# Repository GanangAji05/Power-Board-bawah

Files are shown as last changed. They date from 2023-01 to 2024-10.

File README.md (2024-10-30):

# Power-Board-bawah

Design PCB



Design 3D



Check signal PWM
IMG-20240414-WA0002

Testing Motor and code

https://github.com/user-attachments/assets/2eb00f5d-e821-4132-b0ed-e6486bcefb03

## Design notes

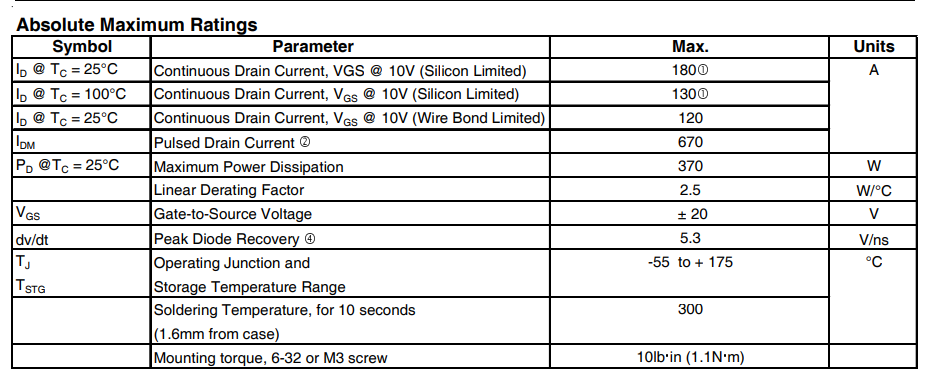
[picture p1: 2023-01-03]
docs/mosfets/irfb4110.png

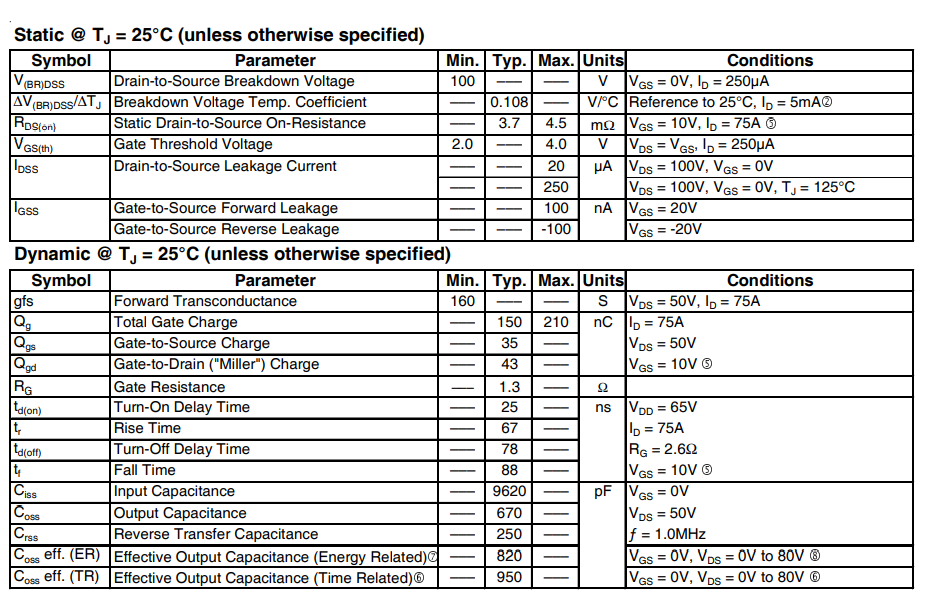
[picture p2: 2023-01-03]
docs/mosfets/irfb4110-2.png

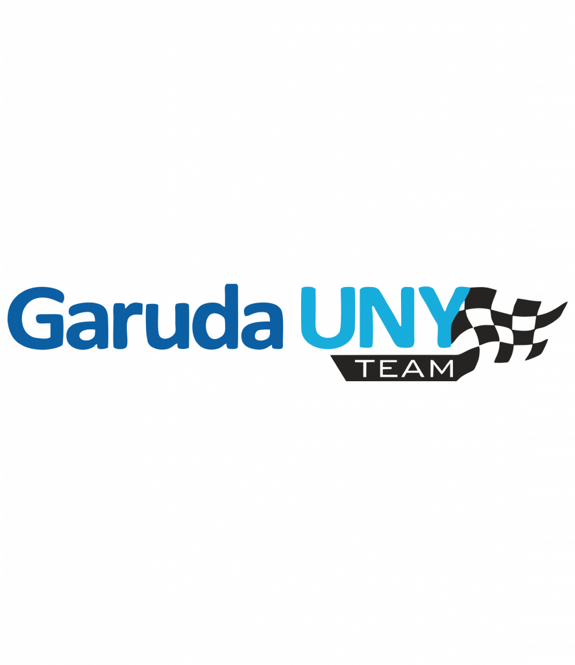
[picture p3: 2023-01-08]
external_cad_lib/garuda-886x1024.png

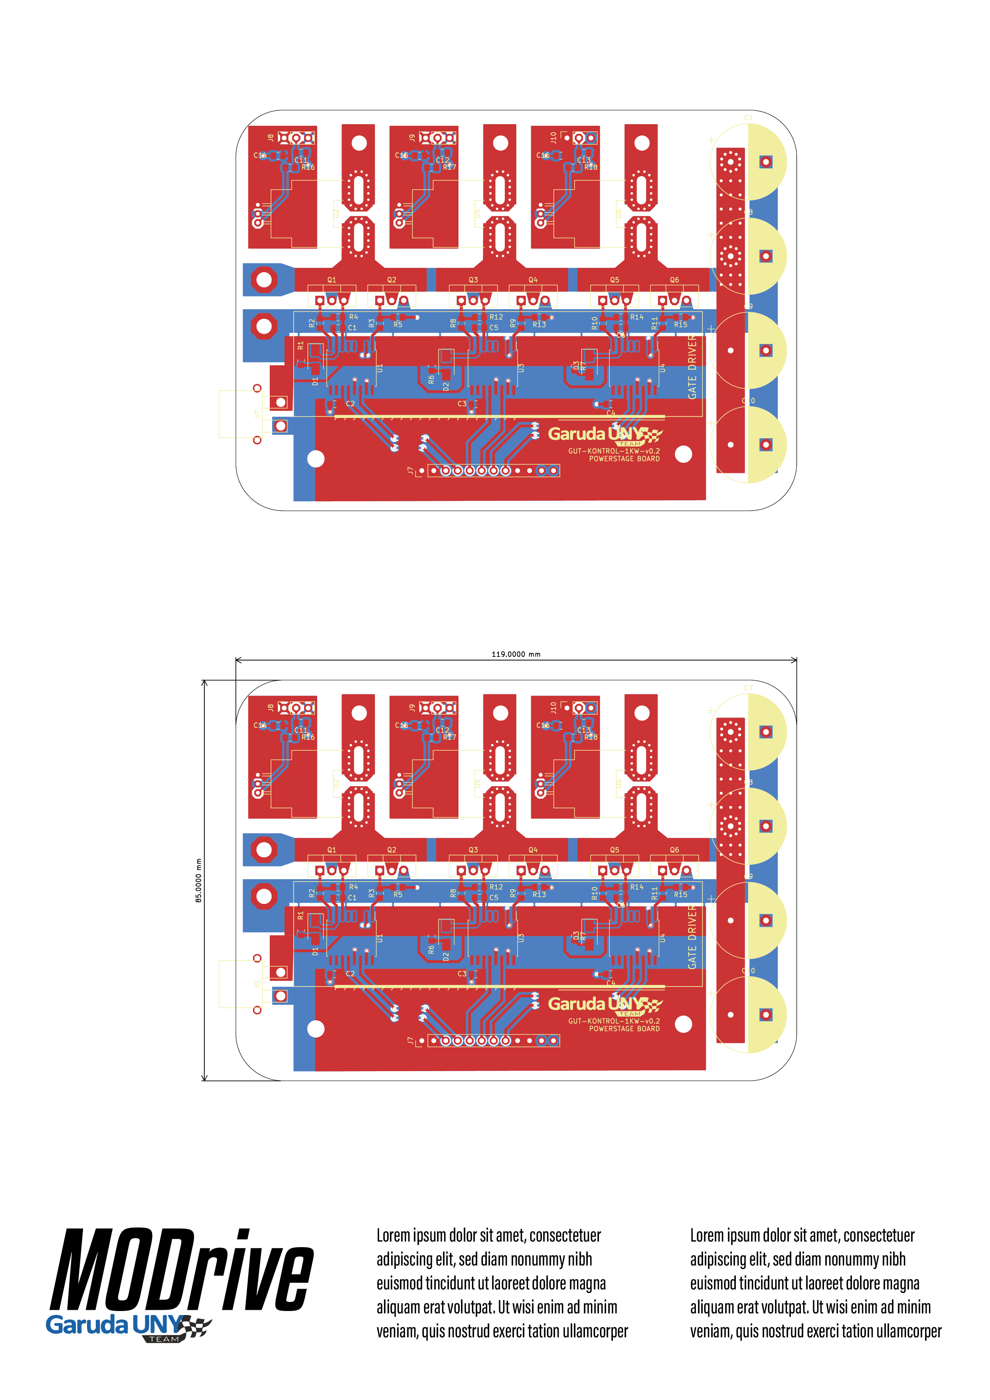
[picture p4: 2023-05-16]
artwork/pcb_artwork-01.png

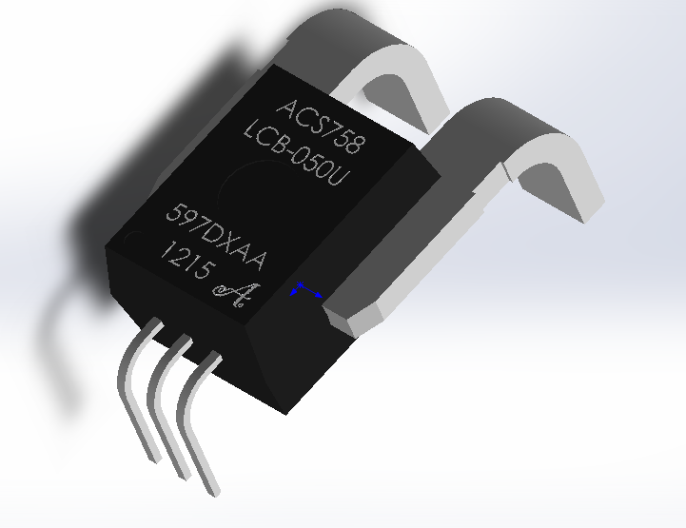
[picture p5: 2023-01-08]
external_cad_lib/acs758-1.snapshot.2/Renderings/Безымянный.png

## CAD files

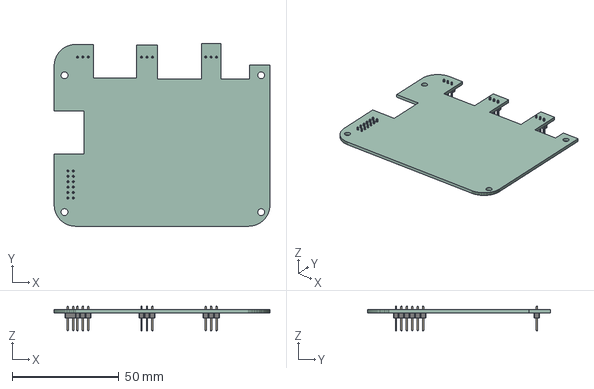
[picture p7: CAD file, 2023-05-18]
dats-kontrol-1kw-sysmin.step
101.0 x 85.4 x 11.5 mm
PCB

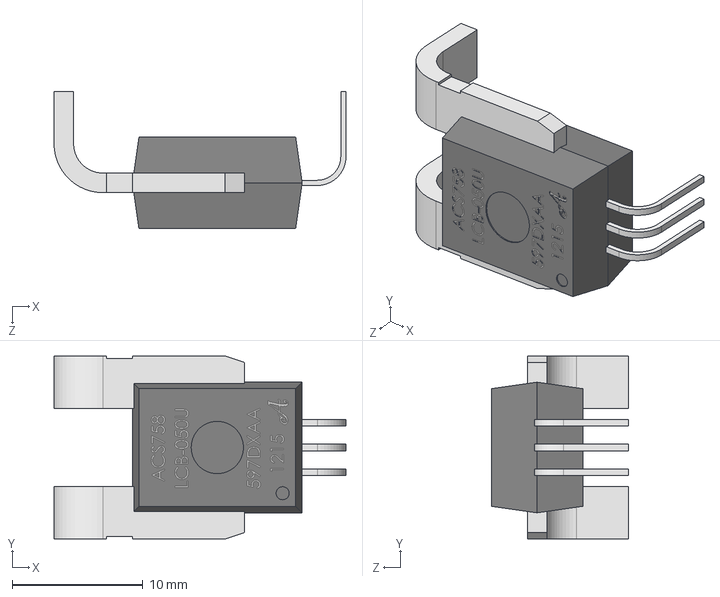
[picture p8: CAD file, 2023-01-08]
external_cad_lib/acs758-1.snapshot.2/ACS758.STEP
22.4 x 14.0 x 10.5 mm

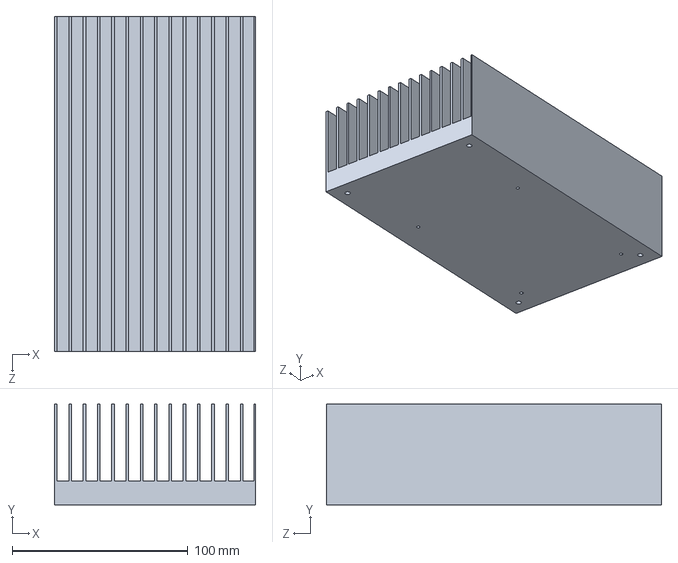
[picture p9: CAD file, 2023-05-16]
external_cad_lib/heatsink.STEP
114.3 x 57.1 x 190.5 mm

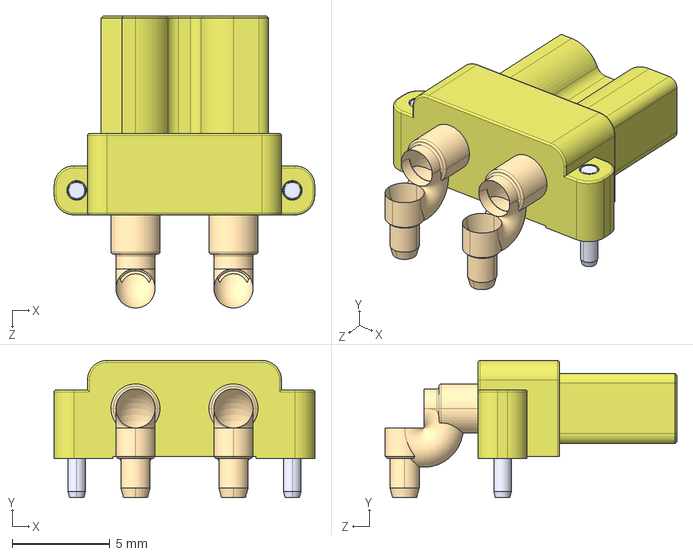
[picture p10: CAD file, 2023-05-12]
external_cad_lib/XT30PW-F/XT30PW-F.step
13.3 x 7.00 x 14.9 mm

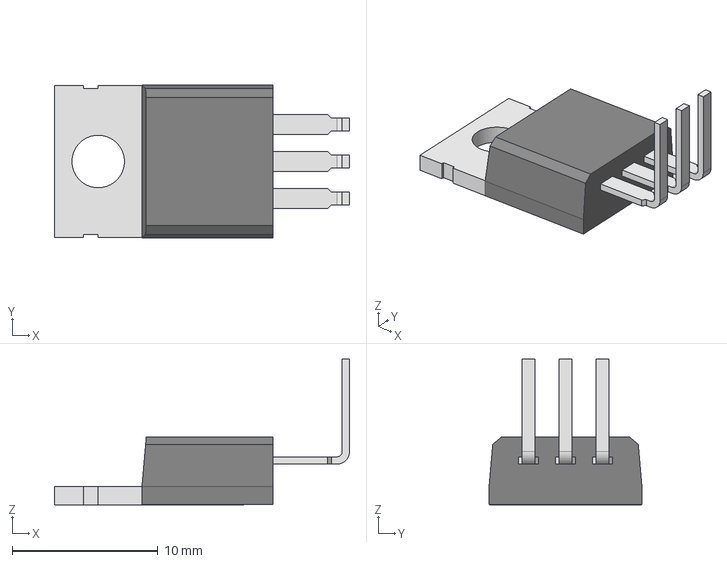
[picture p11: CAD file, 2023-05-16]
external_cad_lib/TO-220_horizontal_back_line.stp
20.2 x 10.5 x 10.0 mm

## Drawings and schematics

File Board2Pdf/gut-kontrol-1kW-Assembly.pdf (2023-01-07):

1 | 2 | 3 | 4 | 5 | 6

A

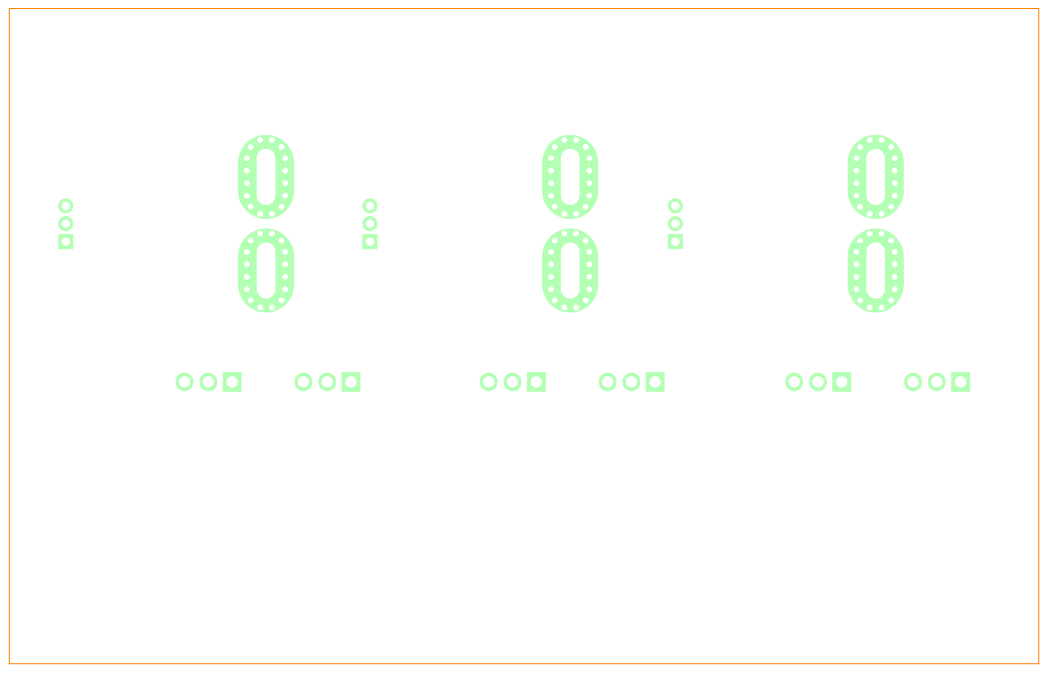
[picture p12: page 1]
D Date: KiCad E.D.A. kicad (6.0.10) Size: A4; Rev:

File: gut-kontrol-1kW.kicad_pcb Sheet: ColoredBottom
Id: 1/1 Title:

1 | 2 | 3 | 4 | 5 | 6

A

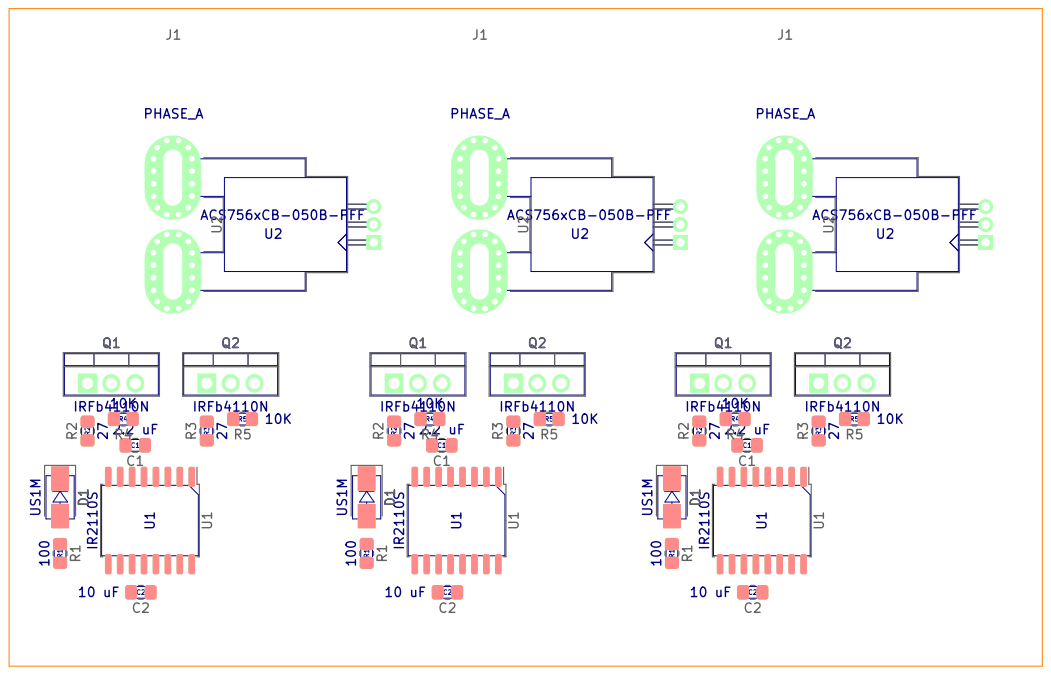
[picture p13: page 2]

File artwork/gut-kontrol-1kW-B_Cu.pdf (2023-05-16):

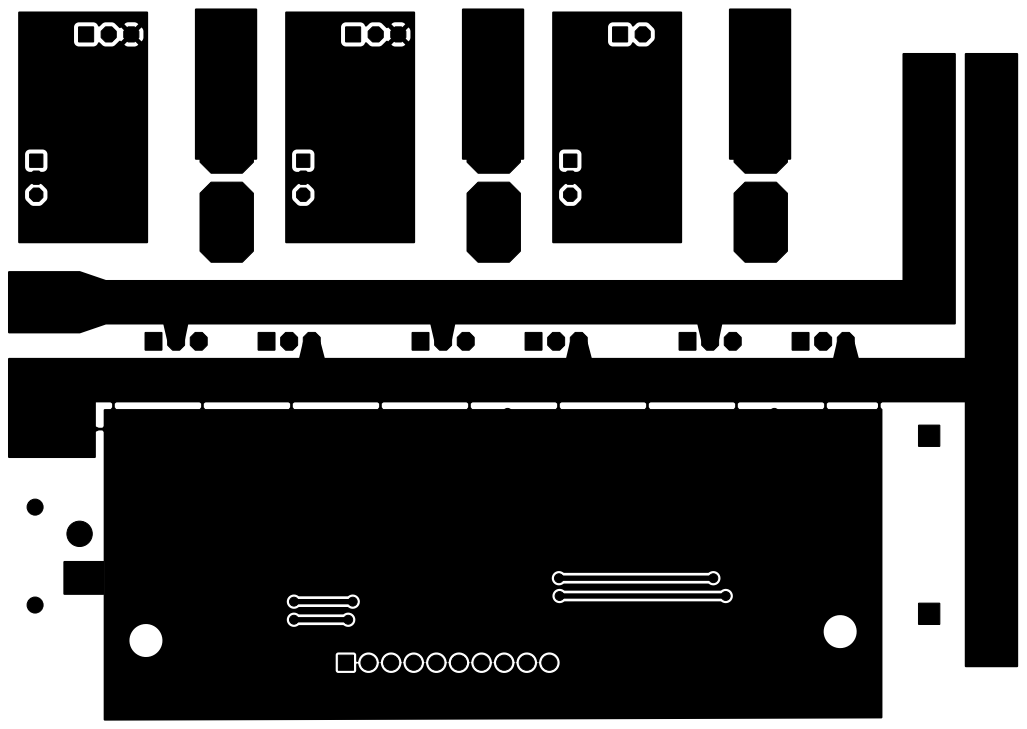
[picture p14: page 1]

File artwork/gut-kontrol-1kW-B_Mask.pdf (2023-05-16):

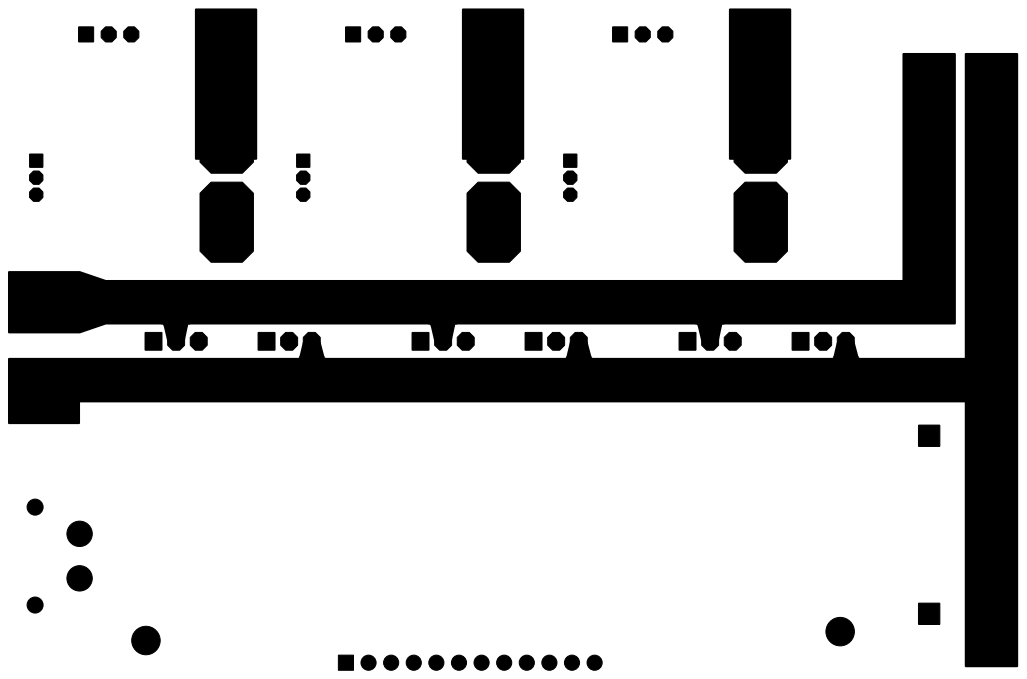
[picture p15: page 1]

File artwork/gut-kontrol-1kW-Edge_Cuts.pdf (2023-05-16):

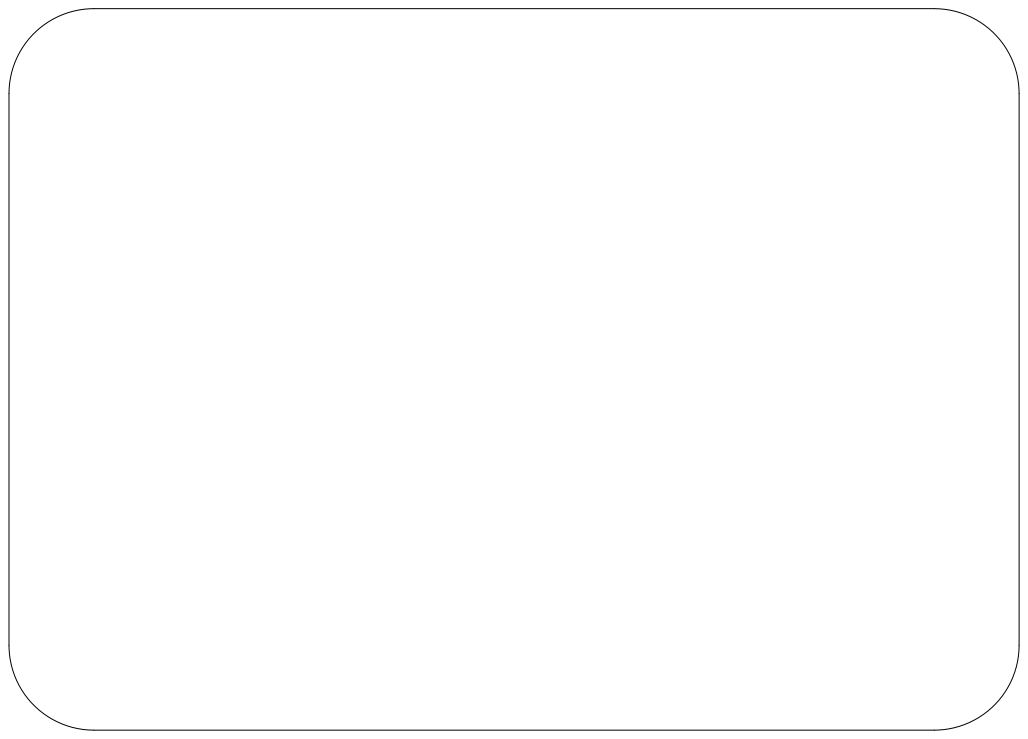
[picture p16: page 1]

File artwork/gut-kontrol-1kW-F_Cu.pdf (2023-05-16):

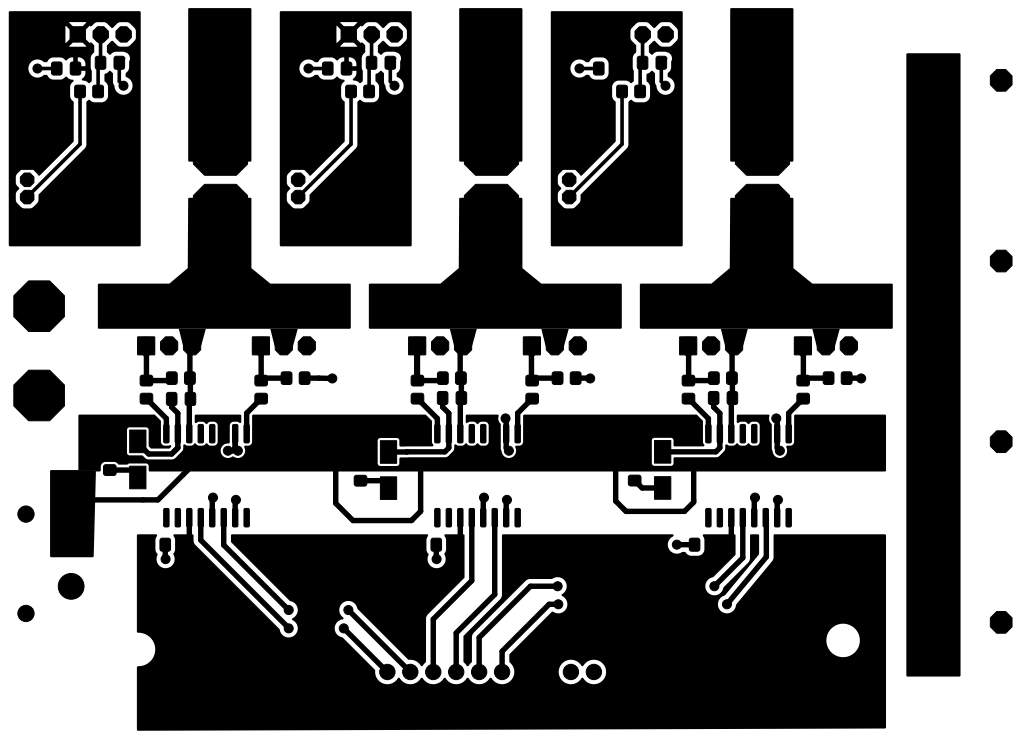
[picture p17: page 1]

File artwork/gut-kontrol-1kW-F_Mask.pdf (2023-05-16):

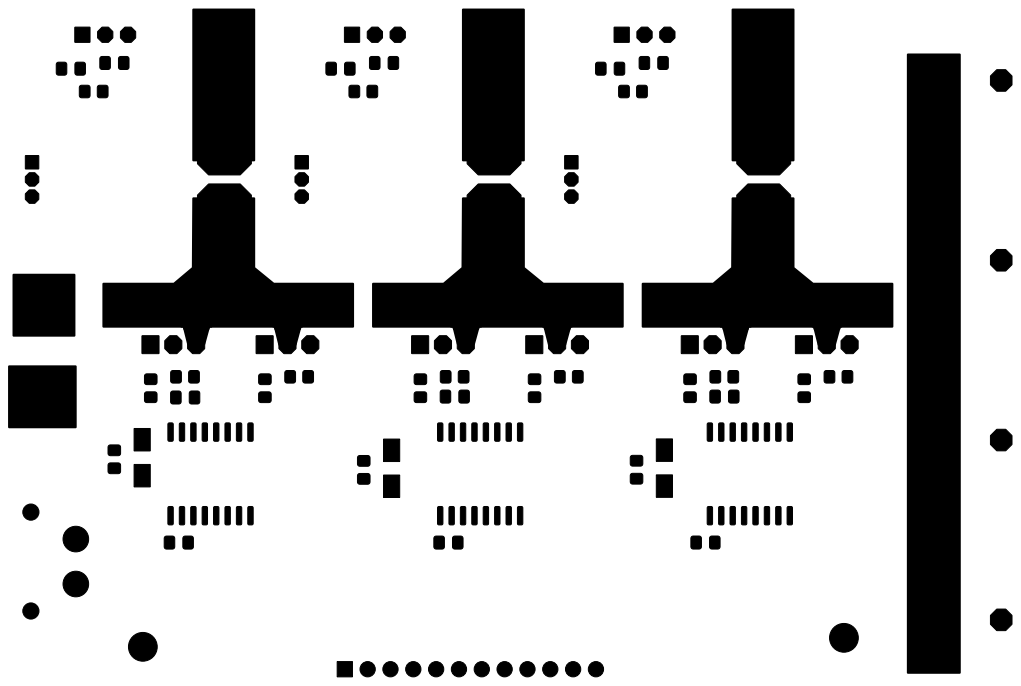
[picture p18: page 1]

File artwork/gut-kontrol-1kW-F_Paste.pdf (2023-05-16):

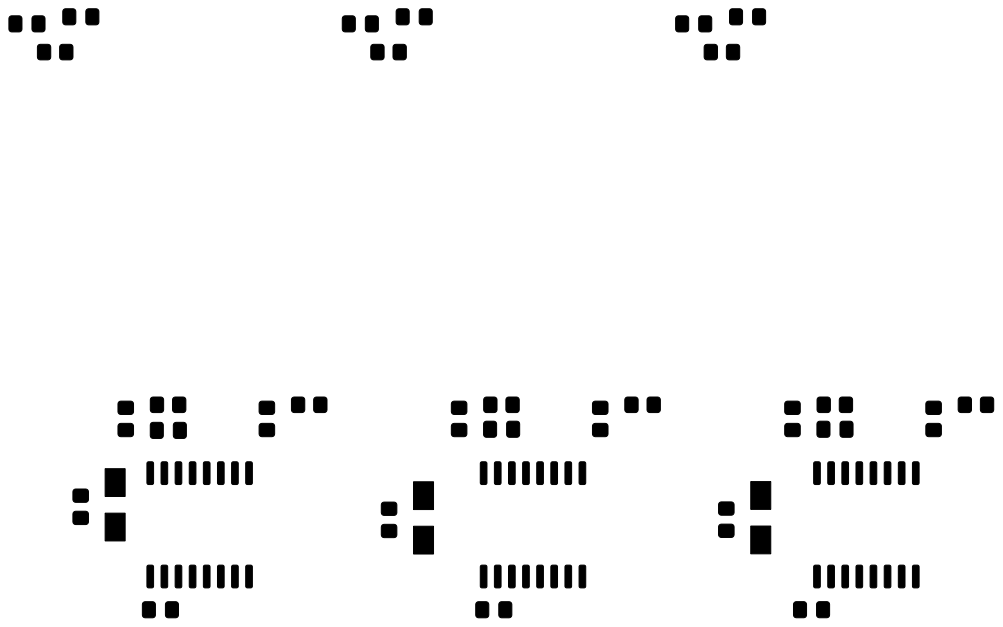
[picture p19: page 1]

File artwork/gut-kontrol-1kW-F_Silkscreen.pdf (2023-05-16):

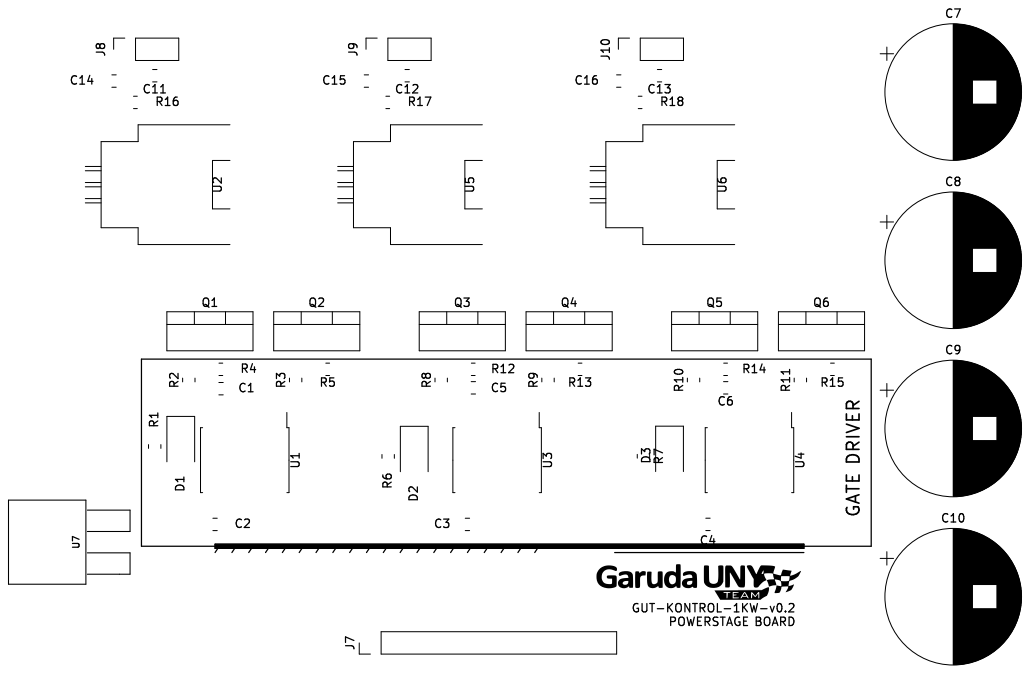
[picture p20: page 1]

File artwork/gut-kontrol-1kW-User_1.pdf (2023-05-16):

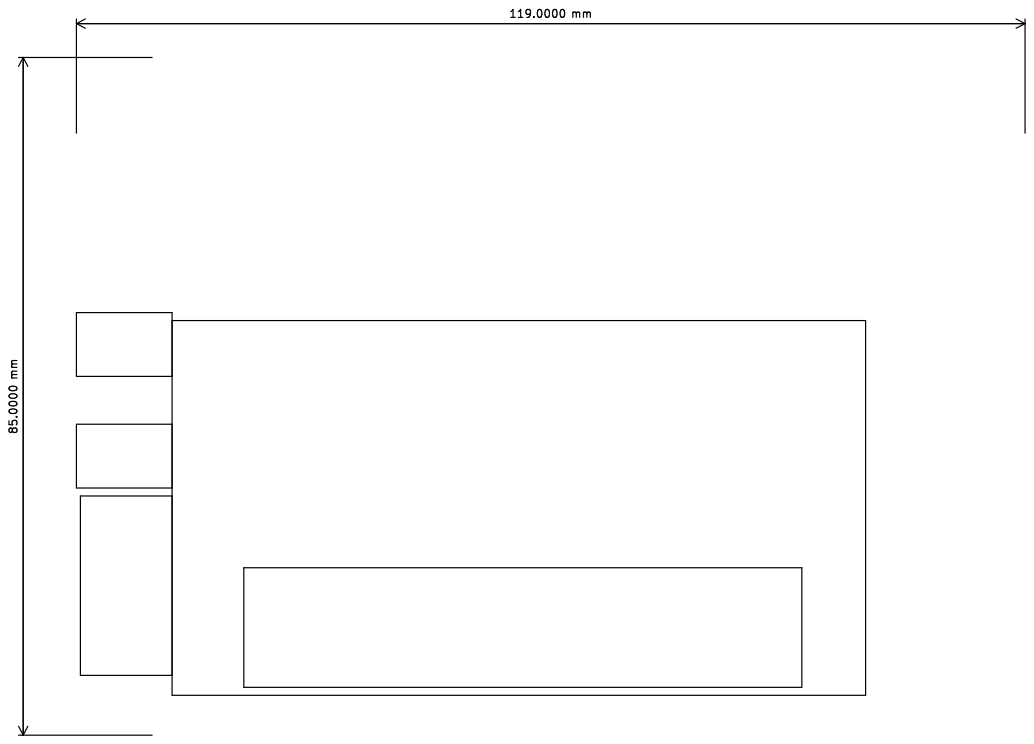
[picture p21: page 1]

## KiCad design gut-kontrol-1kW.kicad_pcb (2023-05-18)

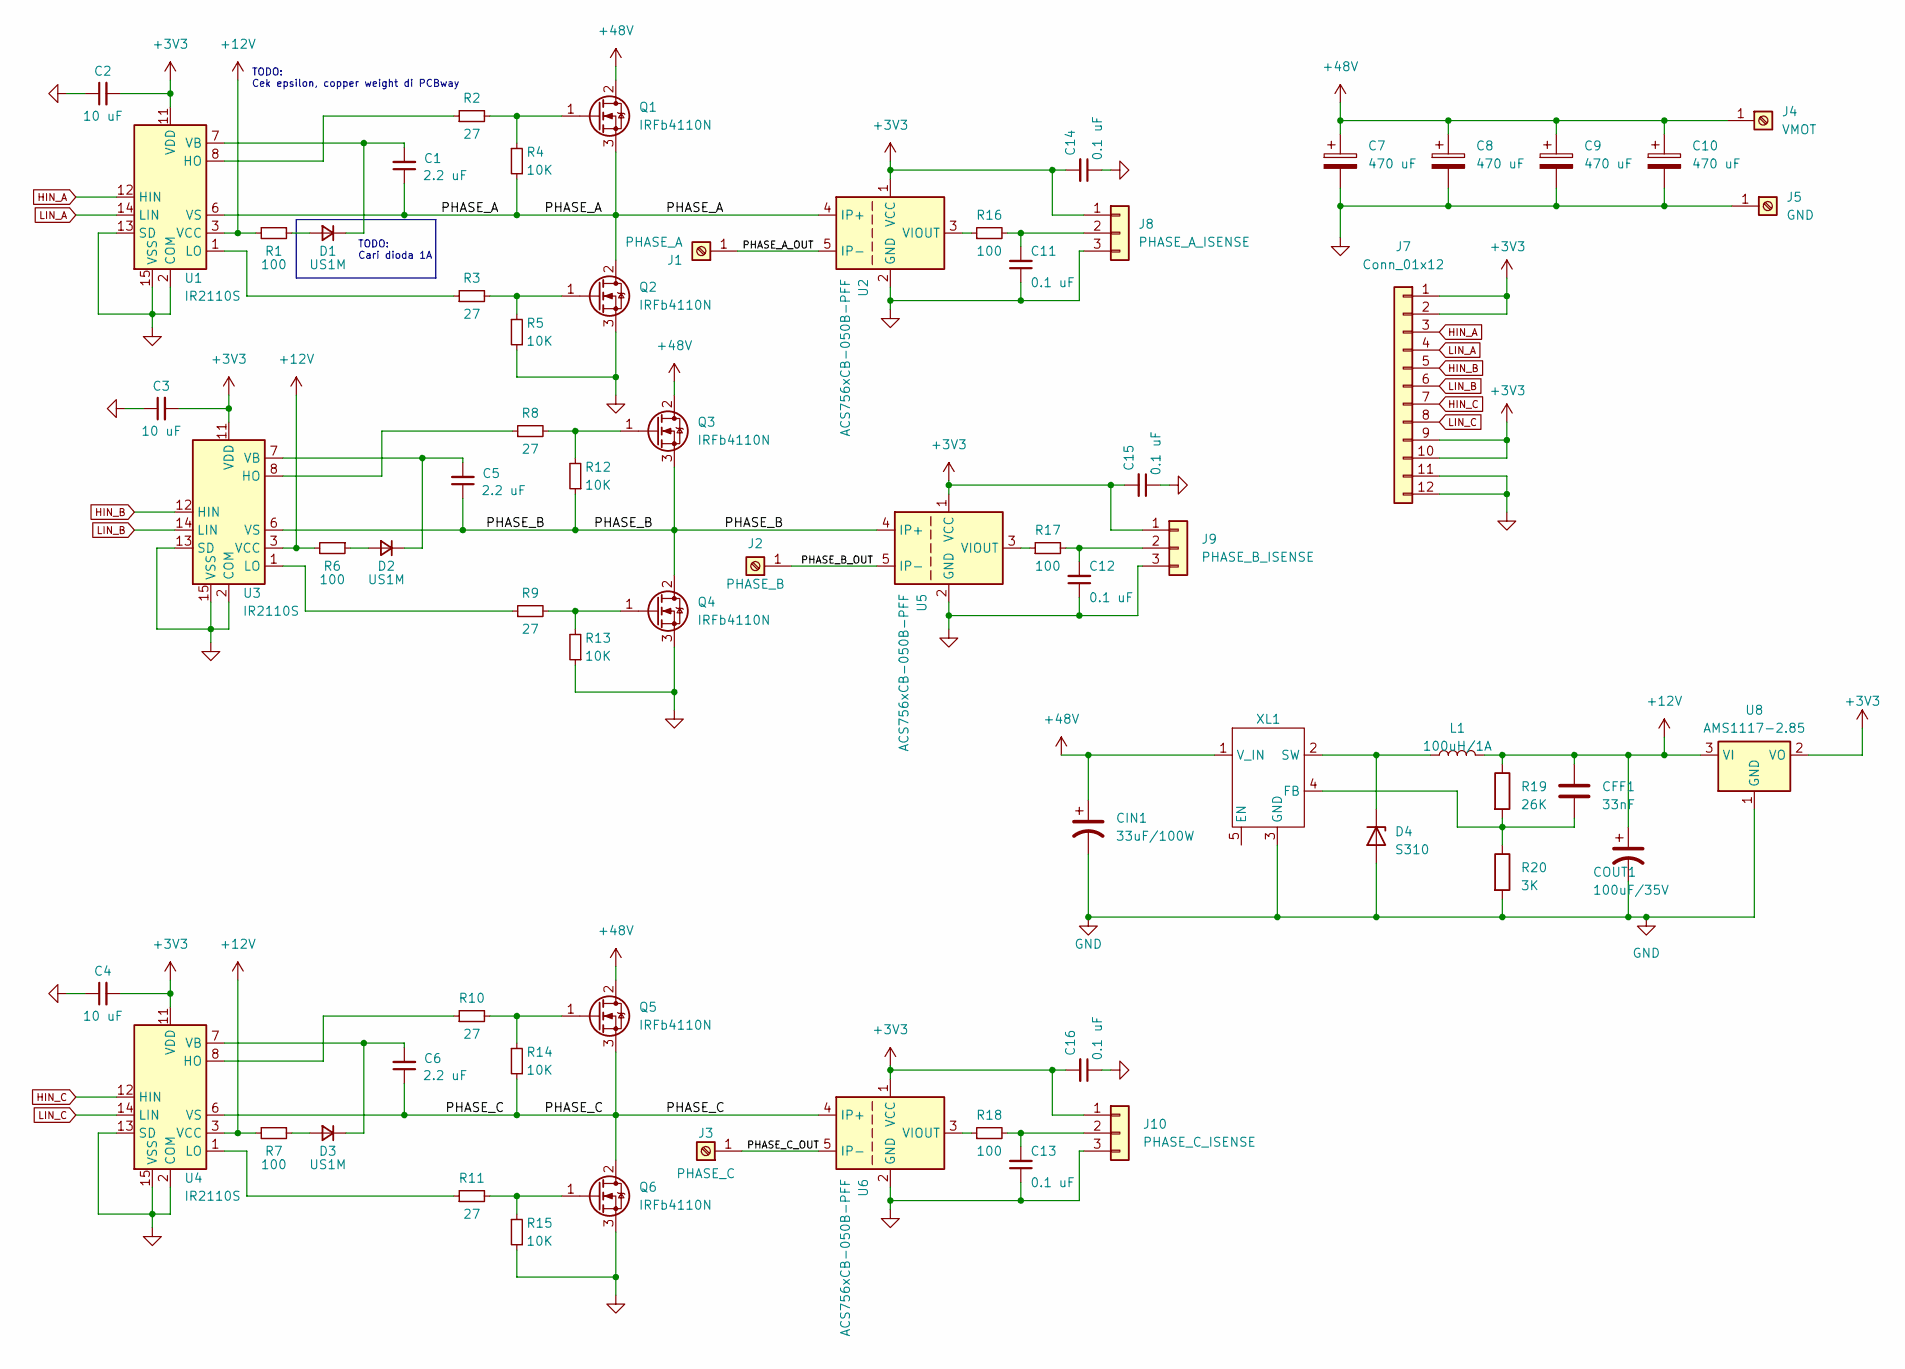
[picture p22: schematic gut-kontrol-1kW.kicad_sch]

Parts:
C1, C5, C6: 2.2 uF; C_0805_2012Metric_Pad1.18x1.45mm_HandSolder
C2, C3, C4: 10 uF; C_0805_2012Metric_Pad1.18x1.45mm_HandSolder
C7, C8, C9, C10: 470 uF; CP_Radial_D16.0mm_P7.50mm
C11, C12, C13, C14, C15, C16: 0.1 uF; C_0805_2012Metric_Pad1.18x1.45mm_HandSolder
CFF1: 33nF; R_0805_2012Metric
CIN1: 33uF/100W; CP_Radial_D8.0mm_P3.50mm
COUT1: 100uF/35V; CP_Radial_D8.0mm_P3.50mm
D1, D2, D3: US1M; D_SMA
D4: S310; D_SMA
J1: PHASE_A; MountingHole_3.2mm_M3_DIN965_Pad
J2: PHASE_B; MountingHole_3.2mm_M3_DIN965_Pad
J3: PHASE_C; MountingHole_3.2mm_M3_DIN965_Pad
J4: VMOT; MountingHole_3.2mm_M3_DIN965_Pad
J5: GND; MountingHole_3.2mm_M3_DIN965_Pad
J7: Conn_01x12; PinHeader_2x06_P2.54mm_Vertical
J8: PHASE_A_ISENSE; PinSocket_1x03_P2.54mm_Vertical
J9: PHASE_B_ISENSE; PinSocket_1x03_P2.54mm_Vertical
J10: PHASE_C_ISENSE; PinSocket_1x03_P2.54mm_Vertical
L1: 100uH/1A; L_10.4x10.4_H4.8
Q1, Q2, Q3, Q4, Q5, Q6: IRFb4110N; TO-220-3_Vertical
R1, R6, R7, R16, R17, R18: 100; R_0805_2012Metric_Pad1.20x1.40mm_HandSolder
R2, R3, R8, R9, R10, R11: 27; R_0805_2012Metric_Pad1.20x1.40mm_HandSolder
R4, R5, R12, R13, R14, R15: 10K; R_0805_2012Metric_Pad1.20x1.40mm_HandSolder
R19: 26K; R_0805_2012Metric
R20: 3K; R_0805_2012Metric
U1, U3, U4: IR2110S; SOIC-16W_7.5x10.3mm_P1.27mm
U2, U5, U6: ACS756xCB-050B-PFF; Allegro_CB_PFF
U8: AMS1117-2.85; SOT-223-3_TabPin2
XL1: TO-252-5_TabPin3

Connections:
+3V3: C2.2, C3.2, C4.2, C14.2, C15.2, C16.2, J7.1, J7.2, J7.9, J7.10, J8.1, J9.1, J10.1, U1.11 (VDD), U2.1 (VCC), U3.11 (VDD), U4.11 (VDD), U5.1 (VCC), U6.1 (VCC), U8.2 (VO)
+12V: CFF1.1, COUT1.1, L1.2, R1.2, R6.2, R7.2, R19.1, U1.3 (VCC), U3.3 (VCC), U4.3 (VCC), U8.3 (VI)
+48V: C7.1, C8.1, C9.1, C10.1, CIN1.1, J4.1, Q1.2 (D), Q3.2 (D), Q5.2 (D), XL1.1 (V_IN)
/PHASE_A: C1.1, Q1.3 (S), Q2.2 (D), R4.1, U1.6 (VS), U2.4 (IP+)
/PHASE_A_OUT: J1.1, U2.5 (IP-)
/PHASE_B: C5.1, Q3.3 (S), Q4.2 (D), R12.1, U3.6 (VS), U5.4 (IP+)
/PHASE_B_OUT: J2.1, U5.5 (IP-)
/PHASE_C: C6.1, Q5.3 (S), Q6.2 (D), R14.1, U4.6 (VS), U6.4 (IP+)
/PHASE_C_OUT: J3.1, U6.5 (IP-)
GND: C2.1, C3.1, C4.1, C7.2, C8.2, C9.2, C10.2, C11.1, C12.1, C13.1, C14.1, C15.1, C16.1, CIN1.2, COUT1.2, D4.2 (A), J5.1, J7.11, J7.12, J8.3, J9.3, J10.3, Q2.3 (S), Q4.3 (S), Q6.3 (S), R5.1, R13.1, R15.1, R20.2, U1.2 (COM), U1.13 (SD), U1.15 (VSS), U2.2 (GND), U3.2 (COM), U3.13 (SD), U3.15 (VSS), U4.2 (COM), U4.13 (SD), U4.15 (VSS), U5.2 (GND), U6.2 (GND), U8.1 (GND), XL1.3 (GND)
HIN_A: J7.3, U1.12 (HIN)
HIN_B: J7.5, U3.12 (HIN)
HIN_C: J7.7, U4.12 (HIN)
LIN_A: J7.4, U1.14 (LIN)
LIN_B: J7.6, U3.14 (LIN)
LIN_C: J7.8, U4.14 (LIN)
unnamed: D1.2 (A), R1.1
unnamed: C1.2, D1.1 (K), U1.7 (VB)
unnamed: D2.2 (A), R6.1
unnamed: C5.2, D2.1 (K), U3.7 (VB)
unnamed: D3.2 (A), R7.1
unnamed: C6.2, D3.1 (K), U4.7 (VB)
unnamed: D4.1 (K), L1.1, XL1.2 (SW)
unnamed: C11.2, J8.2, R16.2
unnamed: C12.2, J9.2, R17.2
unnamed: C13.2, J10.2, R18.2
unnamed: Q1.1 (G), R2.2, R4.2
unnamed: Q2.1 (G), R3.2, R5.2
unnamed: Q3.1 (G), R8.2, R12.2
unnamed: Q4.1 (G), R9.2, R13.2
unnamed: Q5.1 (G), R10.2, R14.2
unnamed: Q6.1 (G), R11.2, R15.2
unnamed: R2.1, U1.8 (HO)
unnamed: R3.1, U1.1 (LO)
unnamed: R16.1, U2.3 (VIOUT)
unnamed: R8.1, U3.8 (HO)
unnamed: R9.1, U3.1 (LO)
unnamed: R10.1, U4.8 (HO)
unnamed: R11.1, U4.1 (LO)
unnamed: R17.1, U5.3 (VIOUT)
unnamed: R18.1, U6.3 (VIOUT)
unnamed: CFF1.2, R19.2, R20.1, XL1.4 (FB)

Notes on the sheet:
TODO: Cek epsilon, copper weight di PCBway
TODO: Cari dioda 1A

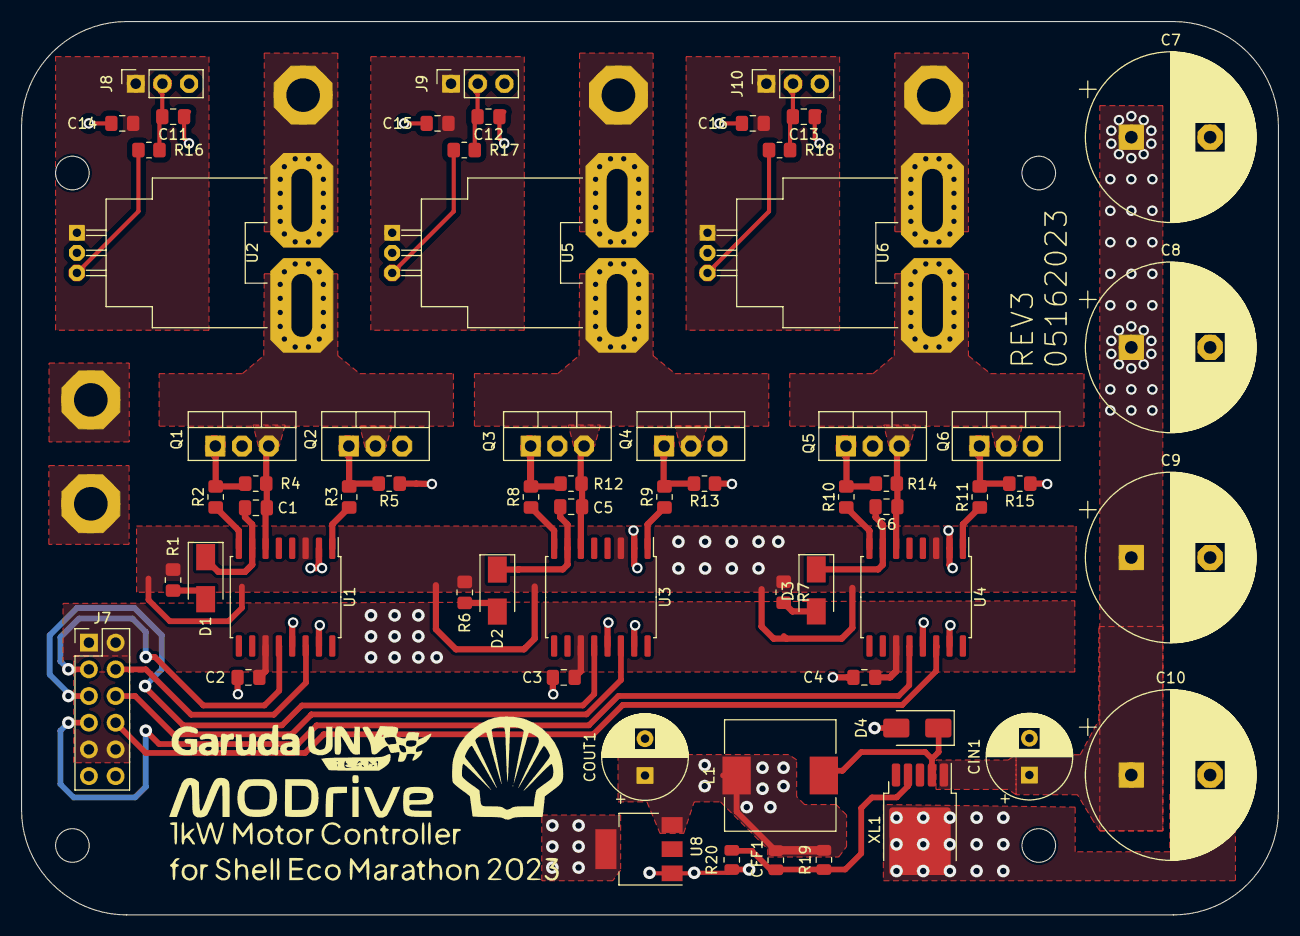
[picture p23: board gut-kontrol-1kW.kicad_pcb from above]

Board: 2 copper layers, 119.6 x 85.0 mm, 67 parts (0 on the bottom side), 42 nets.

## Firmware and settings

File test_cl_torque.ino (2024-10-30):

/**
 * 
 * Torque control example using voltage control loop.
 * 
 * Most of the low-end BLDC driver boards doesn't have current measurement therefore SimpleFOC offers 
 * you a way to control motor torque by setting the voltage to the motor instead of the current. 
 * 
 * This makes the BLDC motor effectively a DC motor, and you can use it in a same way.
 */
#include <SimpleFOC.h>


// BLDC motor & driver instance
// BLDC motor & driver instance
BLDCMotor motor = BLDCMotor(22, 1.2);

// BLDCDriver3PWM driver = BLDCDriver3PWM(pwmA, pwmB, pwmC, Enable(optional));
BLDCDriver6PWM driver = BLDCDriver6PWM(PA8, PB13, PA9, PB14, PA10, PB15);

// Stepper motor & driver instance
//StepperMotor motor = StepperMotor(50);
//StepperDriver4PWM driver = StepperDriver4PWM(9, 5, 10, 6,  8);
int setpoint = 0;
int analog_read = 0;
int avg_setpoint = 0;
// hall sensor instance
HallSensor sensor = HallSensor(PB3, PB4, PB5, 22);

// Interrupt routine intialisation
// channel A and B callbacks
void doA(){sensor.handleA();}
void doB(){sensor.handleB();}
void doC(){sensor.handleC();}


// voltage set point variable
float target_voltage = 0;
// instantiate the commander
Commander command = Commander(Serial);
void doTarget(char* cmd) { command.scalar(&target_voltage, cmd); }

void setup() { 
  
  // initialize encoder sensor hardware
  sensor.init();
  sensor.enableInterrupts(doA, doB, doC); 
  // link the motor to the sensor
  motor.linkSensor(&sensor);

  // driver config
  // power supply voltage [V]
  driver.voltage_power_supply = 24;
  driver.init();
  // link driver
  motor.linkDriver(&driver);

  // aligning voltage
  motor.voltage_sensor_align = 3;
  
  // choose FOC modulation (optional)
  motor.foc_modulation = FOCModulationType::SpaceVectorPWM;

  // set motion control loop to be used
  motor.controller = MotionControlType::torque;

  // use monitoring with serial 
  Serial.begin(115200);
  // comment out if not needed
  motor.useMonitoring(Serial);

  // initialize motor
  motor.init();
  // align sensor and start FOC
  motor.initFOC();

  // add target command T
  command.add('T', doTarget, "target voltage");

  Serial.println(F("Motor ready."));
  Serial.println(F("Set the target voltage using serial terminal:"));
  _delay(1000);
}


void loop() {

  // main FOC algorithm function
  // the faster you run this function the better
  // Arduino UNO loop  ~1kHz
  // Bluepill loop ~10kHz 
  // for(int i = 0; i < 1000; i++){
  //   analog_read = analogRead(PA0);
  //   avg_setpoint += analog_read;
  // }
  // avg_setpoint /= 1000;
  // setpoint = map(avg_setpoint, 0, 1023, 0, 20);
  motor.loopFOC();
  
  // Motion control function
  // velocity, position or voltage (defined in motor.controller)
  // this function can be run at much lower frequency than loopFOC() function
  // You can also use motor.move() and set the motor.target in the code
  motor.move(target_voltage);

  // user communication
  command.run();
}

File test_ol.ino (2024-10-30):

// Open loop motor control example
#include <SimpleFOC.h>


// BLDC motor & driver instance
// BLDCMotor motor = BLDCMotor(pole pair number);
BLDCMotor motor = BLDCMotor(8, 0.4);
// BLDCDriver3PWM driver = BLDCDriver3PWM(pwmA, pwmB, pwmC, Enable(optional));
BLDCDriver6PWM driver = BLDCDriver6PWM(PA8, PB13, PA9, PB14, PA10, PB15);

// Stepper motor & driver instance
//StepperMotor motor = StepperMotor(50);
//StepperDriver4PWM driver = StepperDriver4PWM(9, 5, 10, 6,  8);

//target variable
float target_velocity = 1;

// instantiate the commander
Commander command = Commander(Serial);
void doTarget(char* cmd) { command.scalar(&target_velocity, cmd); }
void doLimit(char* cmd) { command.scalar(&motor.voltage_limit, cmd); }

void setup() {

  // driver config
  // power supply voltage [V]
  driver.pwm_frequency = 10000;
  driver.voltage_power_supply = 30;
  // limit the maximal dc voltage the driver can set
  // as a protection measure for the low-resistance motors    

  
  // this value is fixed on startup
  driver.voltage_limit = 30;
  driver.init();
  // link the motor and the driver
  motor.linkDriver(&driver);

  // limiting motor movements
  // limit the voltage to be set to the motor
  // start very low for high resistance motors
  // current = voltage / resistance, so try to be well under 1Amp
  motor.voltage_limit = 1;   // [V]
 
  // open loop control config
  motor.foc_modulation = FOCModulationType::SpaceVectorPWM;
  motor.controller = MotionControlType::velocity_openloop;
  motor.velocity_limit = 100;

  // init motor hardware
  motor.init();

  // add target command T
  command.add('T', doTarget, "target velocity");
  command.add('L', doLimit, "voltage limit");

  Serial.begin(115200);
  Serial.println("Motor ready!");
  Serial.println("Set target velocity [rad/s]");
  _delay(1000);
}

void loop() {

  // open loop velocity movement
  // using motor.voltage_limit and motor.velocity_limit
  motor.move(target_velocity);

  // user communication
  command.run();
}

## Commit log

2023-01-03 Project Init
    [gut-kontrol-1kW.kicad_pcb, gut-kontrol-1kW.kicad_sch]
2023-01-04 Done with the powerstage
    [gut-kontrol-1kW.kicad_sch]
2023-01-07 done with powerstage board
    [gut-kontrol-1kW.kicad_pcb, gut-kontrol-1kW.kicad_sch]
2023-01-08 Adding connector and CAD viz
    [ACS758.STEP, ACS758.iam, CP_Radial_D16.0mm_P7.50mm.iam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]
2023-01-12 some minor fix
    [gut-kontrol-1kW.kicad_pcb]
2023-05-12 major fix in conn footprint, bootsrap error, etc
    [ACS758.iam, CP_Radial_D16.0mm_P7.50mm.iam, C_0805_2012Metric.iam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]
2023-05-14 Nambah Skematik
    [gut-kontrol-1kW.kicad_sch]
2023-05-14 nambah footprint dikit
2023-05-14 ganti heatsink
    [TO-220_horizontal_back_line.stp, gut-kontrol-1kW.kicad_pcb, gut-kontrol-1kW.kicad_sch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]
2023-05-15 Layout PCB
    [gut-kontrol-1kW.kicad_pcb, gut-kontrol-1kW.kicad_sch]
2023-05-16 adding artwork
    [gut-kontrol-1kW.kicad_pcb]
2023-05-16 revisi power plane + logo
    [gut-kontrol-1kW.kicad_pcb]
2023-05-16 fixing thermal to solid in sensor
    [gut-kontrol-1kW.kicad_pcb]
2023-05-16 nambah rev number
    [gut-kontrol-1kW.kicad_sch]
2023-05-18 adding cad export
    [dats-kontrol-1kw-sysmin.step, gut-kontrol-1kW.kicad_pcb]
